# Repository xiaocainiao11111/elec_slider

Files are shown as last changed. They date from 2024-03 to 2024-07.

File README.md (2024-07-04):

# 基于STM32F103CBT6的电控滑轨设计
>菜鸡毕设

## 文件夹介绍
- 0.STM32程序：使用keil开发，包含全部源码，环境配置看https://zhuanlan.zhihu.com/p/670162318

- 1.QT上位机：QT4.11.1

- 2.原理图和PCB：立创EDA标准版工程

- 3.3D模型：SOLIDWORKS 2023  

# 项目说明

- 项目使用42步进电机作为移动装置，控制程序使用稚晖君dummy中的42闭环程序，使用MT6816作为磁编码器检测角度，电机细分数为256，一圈步数为51200。
- 使用串口通讯
- 使用12V电池作为电源

>资料和说明代补充中。。。

## 参考：

https://zhuanlan.zhihu.com/p/147659820

https://github.com/unlir/XDrive

https://link.zhihu.com/?target=https%3A//github.com/peng-zhihui/Dummy-Robot

https://link.zhihu.com/?target=https%3A//github.com/xiaocainiao11111/Dummy_42_copy

# *make by xiaocainiao*

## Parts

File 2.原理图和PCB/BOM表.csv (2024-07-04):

ID | Name | Designator | Footprint | Quantity | Manufacturer Part | Manufacturer | Supplier | Supplier Part | Price
1 | 0.1u | C1,C2,C3,C5,C6,C7,C8,C10,C21,C22,C25,C26 | C0603 | 12
2 | 100uF | C4,C9,C12,C13 | C1206 | 4 | CL31A107MQHNNNE | SAMSUNG(三星) | LCSC | C15008 | 0.4217
3 | 10nf | C11,C17,C19 | C0603 | 3
4 | 0.1uf | C18 | C0603 | 1
5 | 100pf | C20 | C0603 | 1
6 | 10uf | C23 | C0603 | 1
7 | 10uf/50v | C24 | C0603 | 1
8 | P6SMB6.8CA-C78395 | D1 | SMB_L4.6-W3.6-LS5.3-BI | 1 | P6SMB6.8CA/TR13 | Brightking(君耀电子) | LCSC | C78395 | 0.3096
9 | SS54_C22452 | D2 | SMA_L4.4-W2.8-LS5.4-R-RD | 1 | SS54 | MDD | LCSC | C22452 | 0.2811
10 | B5819WS | D3,D4 | SOD-323_L1.8-W1.3-LS2.5-RD | 2 | B5819WS | Slkor(萨科微) | LCSC | C488405 | 0.0941
11 | CON4_1 | J1 | 排针4PIN | 1
12 | 6.8uH | L1 | IND-SMD_L6.0-W6.0_SWPA6045S | 1 | SWPA6045S6R8MT | Sunlord(顺络) | LCSC | C57254 | 0.4221
13 | 17-21SURC/S530-A3/TR8 | LED1 | LED0805-R-RD | 1 | 17-21SURC/S530-A3/TR8 | EVERLIGHT(亿光) | LCSC | C72037 | 0.1362
14 | TJ-S1608SW6TGLCCW-A5 | LED2 | LED0603-R-RD | 1 | TJ-S1608SW6TGLCCW-A5 | TOGIALED(统佳) | LCSC | C192669 | 0.2173
15 | 10k | R1,R2,R15 | R0603 | 3
16 | 1k | R3,R4,R6,R8 | R0603 | 4
17 | 100mΩ | R5,R9 | R1206 | 2 | 1206W4F100LT5E | UNI-ROYAL(厚声) | LCSC | C25334 | 0.0315
18 | 100 | R7,R14 | R0603 | 2
19 | 120 | R13 | R0603 | 1
20 | 1.8k | R16 | R0603 | 1
21 | 1m | R17 | R0603 | 1
22 | TS-1088R-02526 | SW1,SW2 | SW-SMD_L3.9-W3.0-P4.45 | 2 | TS-1088R-02526 | XUNPU(讯普) | LCSC | C455281 | 0.3356
23 | 测试点 | TP1,TP2,TP3 | 测试点 | 3 |  |  | TKMK
24 | STM32F103CBT6 | U1 | LQFP-48_L7.0-W7.0-P0.50-LS9.0-BL | 1 | STM32F103CBT6 | ST(意法半导体) | LCSC | C8304 | 9.68
25 | TB67H450FNG | U2,U3 | SOP-8_L4.9-W3.9-P1.27-LS6.0-TL-EP | 2 | TB67H450FNG | null | LCSC | C2840040
26 | MT6816CT-AKD | U4 | SOP-8_L5.0-W4.0-P1.27-LS6.0-BL | 1 | MT6816CT-AKD | MagnTek(麦歌恩) | LCSC | C879561 | 17.44
27 | SN65HVD232DR | U5 | SOIC-8_L5.0-W4.0-P1.27-LS6.0-BL | 1 | SN65HVD232DR | TI(德州仪器) | LCSC | C30530 | 4.98
28 | ME3116 | U6 | SOT-23-6_L2.9-W1.6-P0.95-LS2.8-BL | 1 | ME3116AM6G | MICRONE(南京微盟) | LCSC | C97643 | 0.8384
29 | TPLP2992IM5X-3.3 | U7 | SOT-23-5_L2.9-W1.6-P0.95-LS2.8-BL | 1 | TPLP2992IM5X-3.3 | TECH PUBLIC(台舟) | LCSC | C5370974 | 1.3054
30 | Heaer-侧2*4 | U8,U13 | 侧焊2*4排针 | 2
31 | 12MHz | X1 | OSC-SMD_4P-L3.2-W2.5-BL | 1 | X322512MSB4SI | YXC(扬兴晶振) | LCSC | C9002 | 0.403

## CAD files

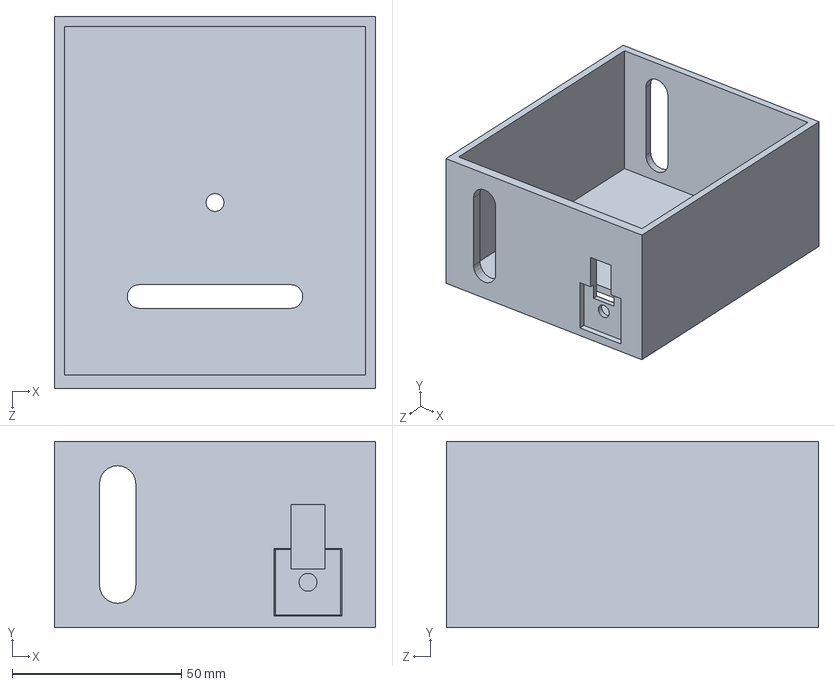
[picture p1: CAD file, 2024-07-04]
3.3D模型/盒子.SLDPRT
95.0 x 55.0 x 110.0 mm

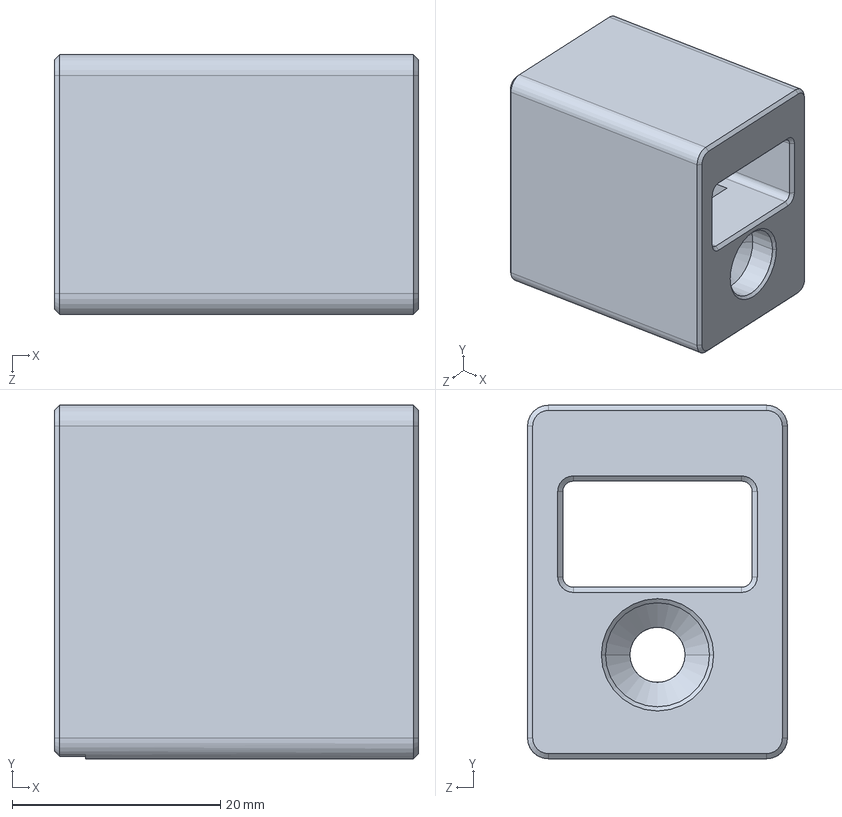
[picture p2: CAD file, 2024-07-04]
3.3D模型/惰轮固定座.SLDPRT
35.0 x 34.0 x 25.0 mm

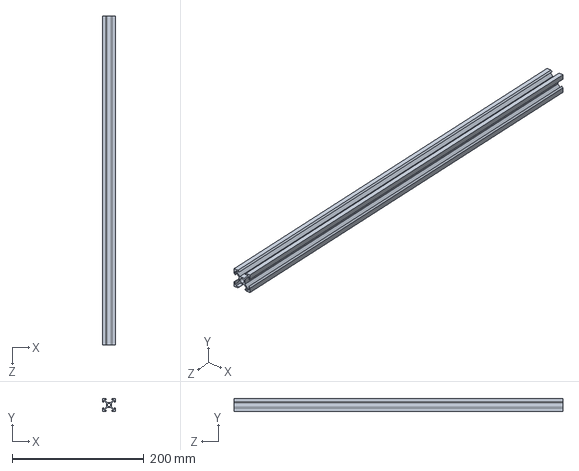
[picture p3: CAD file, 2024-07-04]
3.3D模型/铝材.SLDPRT
20.0 x 20.0 x 500.0 mm

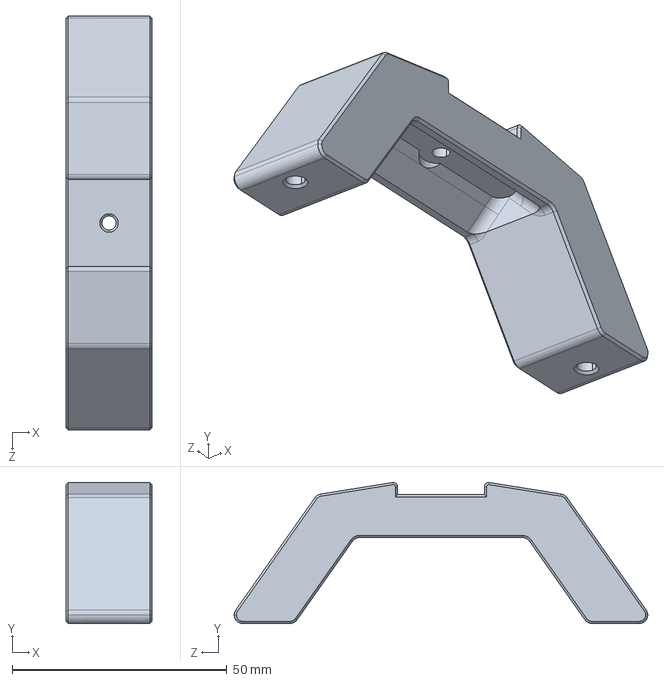
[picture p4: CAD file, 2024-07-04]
3.3D模型/支撑脚.SLDPRT
20.0 x 32.8 x 96.3 mm

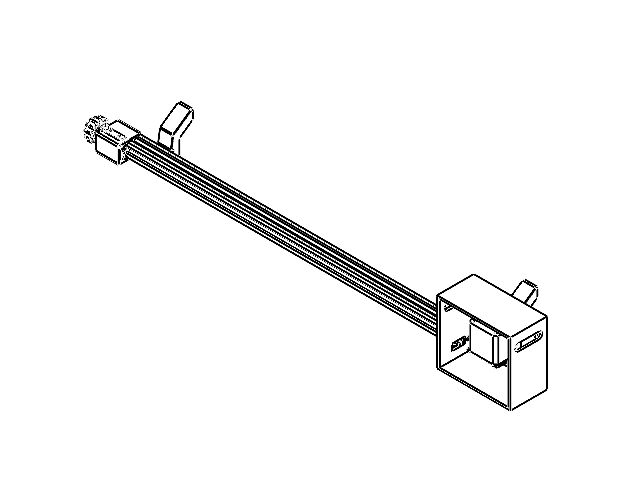
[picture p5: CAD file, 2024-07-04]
3.3D模型/装配体.SLDASM
电机底座
零件1
铝材
盒子
惰轮固定座.step
惰轮旋钮.step
惰轮座.step

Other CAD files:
3.3D模型/惰轮固定座.step.SLDDRW
3.3D模型/支撑脚.SLDDRW
3.3D模型/盒子.SLDDRW
3.3D模型/装配体.SLDDRW
3.3D模型/铝材.SLDDRW

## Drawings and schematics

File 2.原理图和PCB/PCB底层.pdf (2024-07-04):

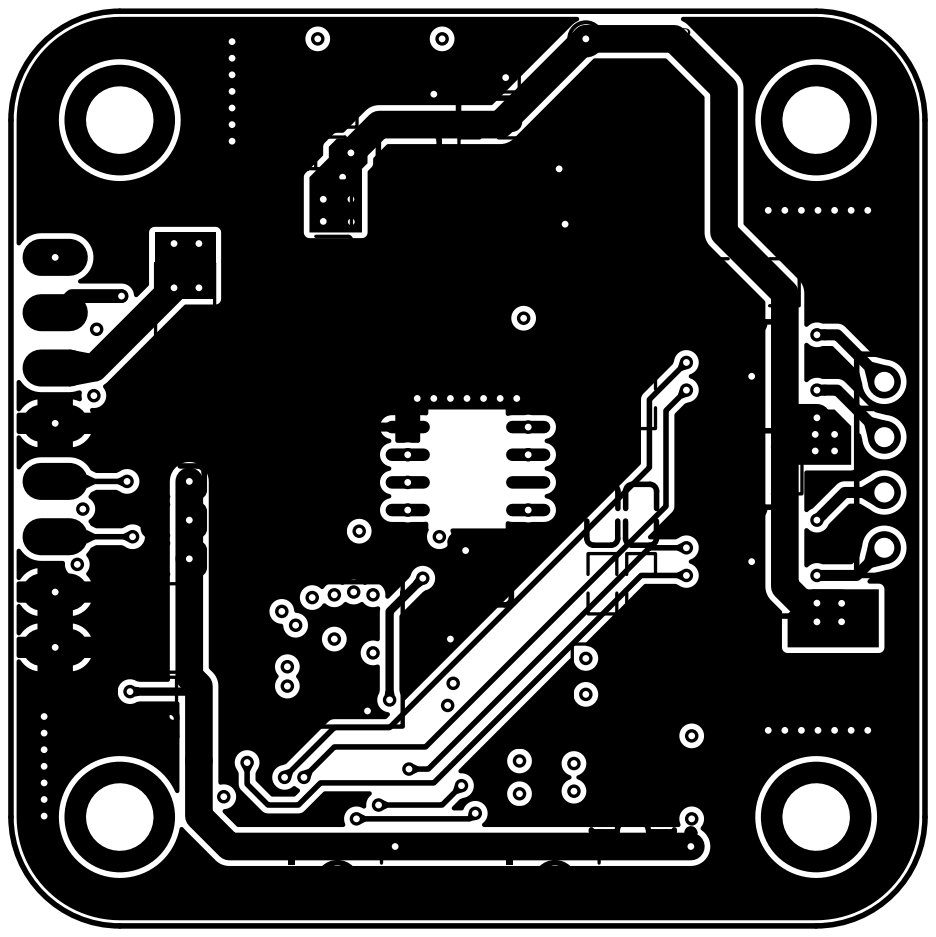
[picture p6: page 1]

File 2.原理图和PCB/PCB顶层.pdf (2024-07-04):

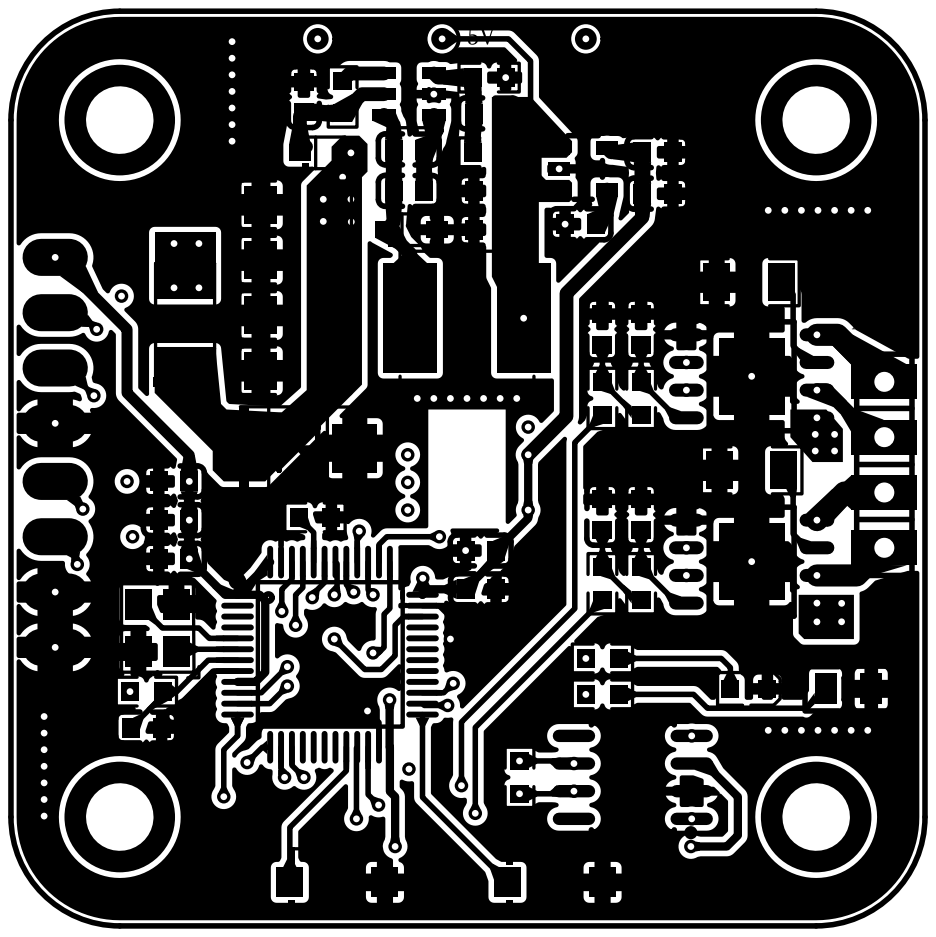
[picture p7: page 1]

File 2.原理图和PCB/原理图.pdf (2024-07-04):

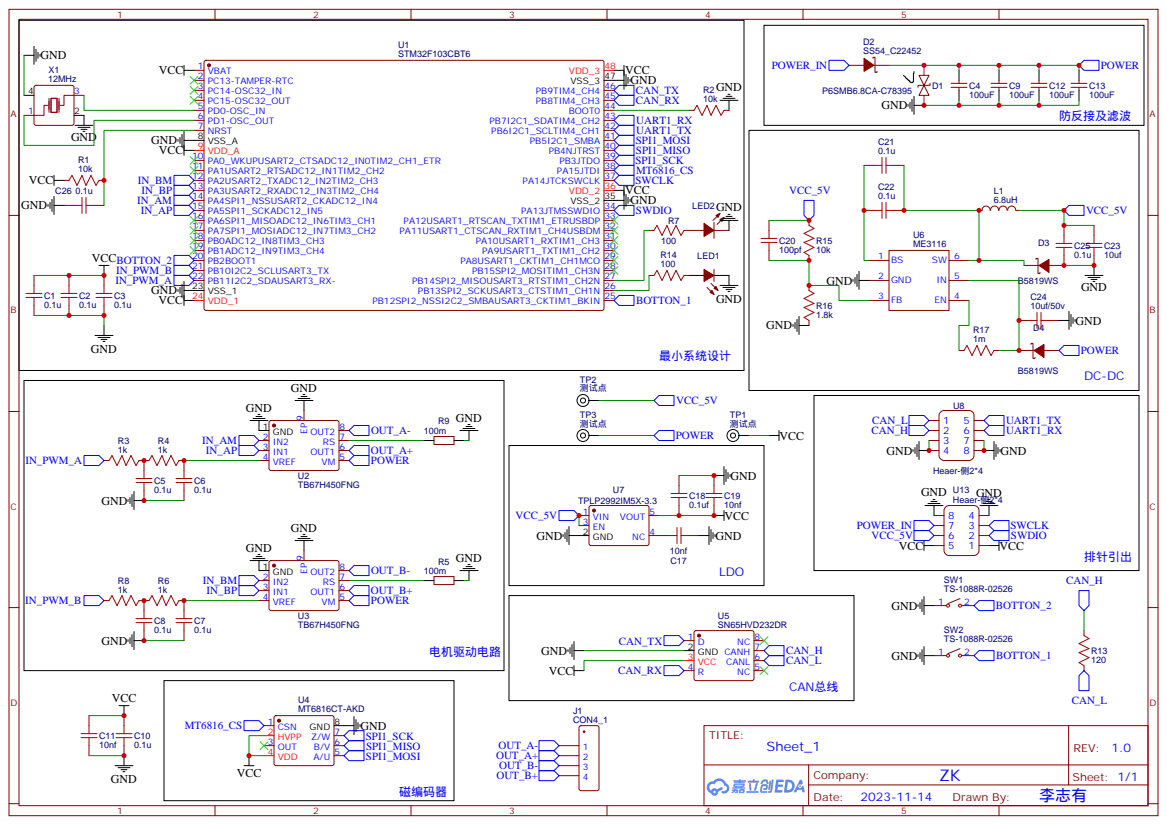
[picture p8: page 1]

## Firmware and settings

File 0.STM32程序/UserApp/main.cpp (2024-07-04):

#include "common_inc.h"
#include "configurations.h"

/*
sqrtf测试，计算平方根
*/

// extern "C"  void tim4callback(void);

extern uint8_t TxData[8];
extern uint8_t RxData[8];

extern CAN_TxHeaderTypeDef TxHeader;
extern CAN_RxHeaderTypeDef RxHeader;

uint16_t _b = 0, _g = 0, _p = 0;
uint8_t rx_buffer[128] = {0}, rxLen = 0;

BoardConfig_t boardConfig;
Motor motor;
MT6816Base mt6816_base((uint16_t *)(0x08017C00));
TB67H450Base tb67h450_base;
EncoderCalibratorBase encoder_calibrator_base;
ButtonBase button1(GPIOB, GPIO_PIN_2, 1, 1000), button2(GPIOB, GPIO_PIN_12, 2, 1000);

extern DMA_HandleTypeDef hdma_usart1_rx;
extern uint8_t _a;
extern uint16_t _v;

uint16_t aaa = 0;
uint8_t rec_buff[100] = {0};

extern "C" void Main()
{
    __HAL_UART_ENABLE_IT(&huart1, UART_IT_IDLE);

    HAL_TIM_Base_Start_IT(&htim1);
    HAL_TIM_Base_Start_IT(&htim4);
    HAL_TIM_PWM_Start(&htim2, TIM_CHANNEL_3);
    HAL_TIM_PWM_Start(&htim2, TIM_CHANNEL_4);


    encoder_calibrator_base.isTriggered = 1;
    encoder_calibrator_base.errorCode = EncoderCalibratorBase::CALI_NO_ERROR;
    encoder_calibrator_base.state = EncoderCalibratorBase::CALI_DISABLE;
    encoder_calibrator_base.goPosition = 0;
    encoder_calibrator_base.rcdX = 0;
    encoder_calibrator_base.rcdY = 0;
    encoder_calibrator_base.resultNum = 0;

    mt6816_base.Init();
    motor.controller->Init();

    // HAL_UART_Receive_DMA(&huart1, rx_buffer, 128);
    HAL_UARTEx_ReceiveToIdle_DMA(&huart1, rec_buff, 100);

    motor.AttachEncoder(&mt6816_base);

    boardConfig = BoardConfig_t{
        .configStatus = CONFIG_OK,
        // .canNodeId = defaultNodeID,
        .encoderHomeOffset = 0,
        .defaultMode = Motor::MODE_COMMAND_POSITION,
        .currentLimit = 1 * 1000,                                     // A
        .velocityLimit = 30 * motor.MOTOR_ONE_CIRCLE_SUBDIVIDE_STEPS, // r/s,51200*30
        .velocityAcc = 1000000,                                       // r/s^2,5120000
        .calibrationCurrent = 2000,
        .dce_kp = 200,
        .dce_kv = 80,
        .dce_ki = 300,
        .dce_kd = 250,
        .enableMotorOnBoot = false,
        .enableStallProtect = false};

    motor.motionPlanner.velocityTracker.SetVelocityAcc(boardConfig.velocityAcc);
    __HAL_TIM_SET_COMPARE(&htim2, TIM_CHANNEL_4, 500);
    __HAL_TIM_SET_COMPARE(&htim2, TIM_CHANNEL_3, 900);

    for (;;)
    {

        encoder_calibrator_base.TickMainLoop();

        // static uint32_t _a = 0;
        // _a++;
        // if (_a == 51200)
        // {
        //     _a = 0;
        // }
        // tb67h450_base.SetFocCurrentVector(_a, 1000);
        // HAL_Delay(100);

        // test1();
        // _g = mt6816_base.test1();
        // motor.encoder->test();
    }
}

extern "C" void HAL_TIM_PeriodElapsedCallback(TIM_HandleTypeDef *htim)
{
    static uint32_t goPosition = 0;
    if (htim == &htim1)
    {
        Upload_estvelocity();
    }
    if (htim == &htim4)
    {
        // if (goPosition <= 51200)
        // {
        //     // 测试：以2000mA电流跑一圈
        //     tb67h450_base.SetFocCurrentVector(goPosition, 1000);
        //     goPosition += 2;
        // }
        // mt6816_base.UpdateAngle();

        if (encoder_calibrator_base.isTriggered)
        {
            encoder_calibrator_base.Tick20kHz();
        }
        else
        {

            motor.Tick20kHz();
        }

        // tim4callback();
    }
}

extern "C" void tim4callback()
{
    // mt6816_base.UpdateAngle();
    _b++;
    if (_b == 1000)
    {
        _b = 0;
    }
    if (_b == 1)
    {
        _p++;
        if (_p == 1000)
        {
            _p = 0;
        }
    }
}

void test2()
{
    _g++;
    if (_g == 100)
    {
        _g = 0;
    }
}

void HAL_UART_RxCpltCallback(UART_HandleTypeDef *huart)
{
    uint32_t temp = __HAL_DMA_GET_COUNTER(&hdma_usart1_rx);
    rxLen = 128 - temp;

    HAL_UART_Receive_DMA(&huart1, rx_buffer, 128);
}

void HAL_CAN_RxFifo0MsgPendingCallback(CAN_HandleTypeDef *CanHandle)
{
    /* Get RX message */
    if (HAL_CAN_GetRxMessage(CanHandle, CAN_RX_FIFO0, &RxHeader, RxData) != HAL_OK)
    {
        /* Reception Error */
        Error_Handler();
    }

    uint8_t id = (RxHeader.StdId >> 7);  // 4Bits ID & 7Bits Msg
    uint8_t cmd = RxHeader.StdId & 0x7F; // 4Bits ID & 7Bits Msg
    if (id == 0 || id == 1)
    {
        OnCanCmd(cmd, RxData, RxHeader.DLC);
    }
}

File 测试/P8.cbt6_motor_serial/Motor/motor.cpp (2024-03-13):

// #include "configurations.h"
#include "motor.h"
#include <cmath>
#include "mt6816_base.h"
#include "configurations.h"
#include "tb67h450_base.h"

void Motor::Tick20kHz()
{
    // 1.Encoder data Update，获取mt6816校准值
    mt6816_base.UpdateAngle();

    // 2.Motor Control Update
    CloseLoopControlTick();
}

void Motor::AttachEncoder(MT6816Base *_encoder)
{
    encoder = _encoder;
}

// void Motor::AttachDriver(DriverBase *_driver)
// {
//     driver = _driver;
// }

/*
主闭环控制，第一次运行获取mt6816数据对应细分数，
*/
void Motor::CloseLoopControlTick()
{
    /************************************ First Called ************************************/
    static bool isFirstCalled = true; // static只赋值一次，下次调用不再赋值，并在值变化时保持变量的持久性
    if (isFirstCalled)                // 初次跑闭环，把大半圈位置置负数，比如0到10中把7变-3
    {
        int32_t angle; // 整形有负数
        if (config.motionParams.encoderHomeOffset < MOTOR_ONE_CIRCLE_SUBDIVIDE_STEPS / 2)
        {
            angle =
                encoder->angleData.rectifiedAngle >
                        config.motionParams.encoderHomeOffset + MOTOR_ONE_CIRCLE_SUBDIVIDE_STEPS / 2
                    ? encoder->angleData.rectifiedAngle - MOTOR_ONE_CIRCLE_SUBDIVIDE_STEPS
                    : encoder->angleData.rectifiedAngle;
        }
        else
        {
            angle =
                encoder->angleData.rectifiedAngle <
                        config.motionParams.encoderHomeOffset - MOTOR_ONE_CIRCLE_SUBDIVIDE_STEPS / 2
                    ? encoder->angleData.rectifiedAngle + MOTOR_ONE_CIRCLE_SUBDIVIDE_STEPS
                    : encoder->angleData.rectifiedAngle;
        }

        controller->realLapPosition = angle;
        controller->realLapPositionLast = angle;
        controller->realPosition = angle;
        controller->realPositionLast = angle;

        isFirstCalled = false;
        return;
    }

    /********************************* Update Data *********************************/
    int32_t deltaLapPosition;

    // Read Encoder data
    controller->realLapPositionLast = controller->realLapPosition;   // 上次细分数
    controller->realLapPosition = encoder->angleData.rectifiedAngle; // 当前细分数

    // 注意以下都是以细分数进行
    //  Lap-Position calculate
    deltaLapPosition = controller->realLapPosition - controller->realLapPositionLast; // 与上次细分差
    if (deltaLapPosition > MOTOR_ONE_CIRCLE_SUBDIVIDE_STEPS >> 1)
        deltaLapPosition -= MOTOR_ONE_CIRCLE_SUBDIVIDE_STEPS;
    else if (deltaLapPosition < -MOTOR_ONE_CIRCLE_SUBDIVIDE_STEPS >> 1)
        deltaLapPosition += MOTOR_ONE_CIRCLE_SUBDIVIDE_STEPS;

    // Naive-Position calculate
    controller->realPositionLast = controller->realPosition;
    controller->realPosition += deltaLapPosition;

    /********************************* Estimate Data *********************************/
    // Estimate Velocity
    controller->estVelocityIntegral += ((controller->realPosition - controller->realPositionLast) * motionPlanner.CONTROL_FREQUENCY + ((controller->estVelocity << 5) - controller->estVelocity)); // 位置差值*20000+estVelocity*31累加

    controller->estVelocity = controller->estVelocityIntegral >> 5;    // estVelocityIntegral / 32
    controller->estVelocityIntegral -= (controller->estVelocity << 5); // (位置差值*20000+estVelocity*31)-(位置差值*20000+estVelocity*31)/32*32

    // Estimate Position
    controller->estLeadPosition = Controller::CompensateAdvancedAngle(controller->estVelocity);
    controller->estPosition = controller->realPosition + controller->estLeadPosition; // 由估计速度和补偿表得到估计位置

    // Estimate Error
    controller->estError = controller->softPosition - controller->estPosition;

    /************************************ Ctrl Loop ************************************/
    // if (controller->isStalled ||
    //     controller->softDisable ||
    //     !mt6816_base.IsCalibrated()) // 首次会进入
    // {
    //     controller->ClearIntegral(); // clear integrals
    //     controller->focPosition = 0; // clear outputs
    //     controller->focCurrent = 0;
    //     tb67h450_base.Sleep();
    // }

    static bool _flag1 = 0;
    if (_flag1 == 0)
    {
        controller->ClearIntegral(); // clear integrals
        controller->focPosition = 0; // clear outputs
        controller->focCurrent = 0;
        tb67h450_base.Sleep();
        _flag1 = 1;
    }

    else if (controller->softBrake)
    {
        controller->ClearIntegral();
        controller->focPosition = 0;
        controller->focCurrent = 0;
        tb67h450_base.Brake();
    }
    else
    {
        // controller->requestMode = MODE_COMMAND_VELOCITY;

        // controller->goalVelocity = 51200*4;
        // controller->goalPosition = 51200*2;
        switch (controller->modeRunning)
        {
        case MODE_STEP_DIR:
            controller->CalcDceToOutput(controller->softPosition, controller->softVelocity);
            break;
        case MODE_STOP:
            tb67h450_base.Sleep();
            break;
        case MODE_COMMAND_Trajectory:
            controller->CalcDceToOutput(controller->softPosition, controller->softVelocity);
            break;
        case MODE_COMMAND_CURRENT:
            controller->CalcCurrentToOutput(controller->softCurrent);
            break;
        case MODE_COMMAND_VELOCITY:
            controller->CalcPidToOutput(controller->softVelocity);
            // controller->CalcPidToOutput(200000);
            break;
        case MODE_COMMAND_POSITION:
            controller->CalcDceToOutput(controller->softPosition, controller->softVelocity);
            // controller->CalcDceToOutput(2000, 1000);
            break;
        case MODE_PWM_CURRENT:
            controller->CalcCurrentToOutput(controller->softCurrent);
            break;
        case MODE_PWM_VELOCITY:
            controller->CalcPidToOutput(controller->softVelocity);
            break;
        case MODE_PWM_POSITION:
            controller->CalcDceToOutput(controller->softPosition, controller->softVelocity);
            break;
        default:
            break;
        }
    }

    /******************************* Mode Change Handle ，模式有变  *******************************/
    if (controller->modeRunning != controller->requestMode) //
    {
        controller->modeRunning = controller->requestMode;
        controller->softNewCurve = true;
    }

    /******************************* Update Hard-Goal，限制速度和电流 *******************************/
    if (controller->goalVelocity > config.motionParams.ratedVelocity)
        controller->goalVelocity = config.motionParams.ratedVelocity;
    else if (controller->goalVelocity < -config.motionParams.ratedVelocity)
        controller->goalVelocity = -config.motionParams.ratedVelocity;
    if (controller->goalCurrent > config.motionParams.ratedCurrent)
        controller->goalCurrent = config.motionParams.ratedCurrent;
    else if (controller->goalCurrent < -config.motionParams.ratedCurrent)
        controller->goalCurrent = -config.motionParams.ratedCurrent;
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

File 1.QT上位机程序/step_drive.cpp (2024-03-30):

#include "step_drive.h"
#include "ui_step_drive.h"
#include "widget.h"
#include "thread/thread_1.h"


step_drive::step_drive(QWidget *parent) :
    QWidget(parent),
    ui(new Ui::step_drive)
{
    ui->setupUi(this);
    ui->motor_cali->setEnabled(1);
    ui->estvelocity_slider->setEnabled(0);

    ui->speed_slider->setMaximum(3000);//对应0到30(r/s)
    ui->speed_slider->setMinimum(-3000);
    ui->speed_slider->setValue(0);
    ui->speed_lineedit->setText(QString::number(0));

    ui->position_slider->setMaximum(5000);
    ui->position_slider->setMinimum(-5000);
    ui->position_slider->setValue(0);
    ui->position_lineedit->setText(QString::number(0));

    ui->estvelocity_slider->setMaximum(30000);//对应0到30(r/s)
    ui->estvelocity_slider->setMinimum(-30000);

    _t=new Thread_1;
    _t->start();//开启新线程

    connect(ui->speed_slider,SIGNAL(valueChanged(int)),this,SLOT(speed_ValueChanged(int)));
    connect(ui->position_slider,SIGNAL(valueChanged(int)),this,SLOT(position_ValueChanged(int)));
    connect(this->_t,&Thread_1::get_estvelocity,this,[=](uint16_t _v){
        ui->estvelocity_slider->setValue(_v-30000);
        ui->estspeed_lineedit->setText(QString::number(((float)_v-30000)/1000));
//        qDebug()<<"AAA";
    });


}

step_drive::~step_drive()
{
    delete ui;
}

void step_drive::on_motor_connect_clicked()
{

}

void step_drive::on_motor_init_clicked()
{

}


void step_drive::speed_ValueChanged(int val)
{
    uint8_t tx_speed_data[5]={0xAA,0x55,0x04,0x00,0x00};
    ui->speed_lineedit->setText(QString::number((float)val/100));//int转String
    tx_speed_data[3]=(uint8_t)((val+3000)>>8);
    tx_speed_data[4]=(uint8_t)val+3000;
    serialport->write((char *)tx_speed_data,5);

}

void step_drive::position_ValueChanged(int val)
{
    uint8_t tx_speed_data[5]={0xAA,0x55,0x01,0x00,0x00};
    ui->position_lineedit->setText(QString::number(val));//int转String
    tx_speed_data[3]=(uint8_t)(val+5000>>8);
    tx_speed_data[4]=(uint8_t)val+5000;
    serialport->write((char *)tx_speed_data,5);

}


void step_drive::on_get_velocity_button_clicked()
{
    static bool get_velocity_flag=0;
    uint8_t tx_get_velocity_data[4]= {0xAA,0x55,0x22,0x00};
    get_velocity_flag=!get_velocity_flag;
    ui->estvelocity_slider->setEnabled(1);
    if(get_velocity_flag)
    {
        tx_get_velocity_data[3]=0x01;
    }

    serialport->write((char *)tx_get_velocity_data,4);
    serialport->waitForBytesWritten(10);
}

void step_drive::on_motor_cali_clicked()
{
    uint8_t tx_cali_data[5]={0xAA,0x55,0x02,0x00,0x00};
    serialport->write((char *)tx_cali_data,5);
}
